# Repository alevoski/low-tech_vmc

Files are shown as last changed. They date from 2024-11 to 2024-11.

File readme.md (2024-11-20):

# low-tech_vmc




low-tech_vmc est un projet de construction de VMC double flux de façon low-tech.  
Ce repo présente essentiellement la partie électronique du projet, à base d'Arduino.

Pour avoir tout le détail, notamment la fabrication des caissons, voir cette page :  
https://wiki.lowtechlab.org/wiki/VMC_double_flux

Ce projet a commencé en Janvier 2023.  
C++ est utilisé pour l'ensemble du code source.  
C'est un projet finalisé sujet à des améliorations.

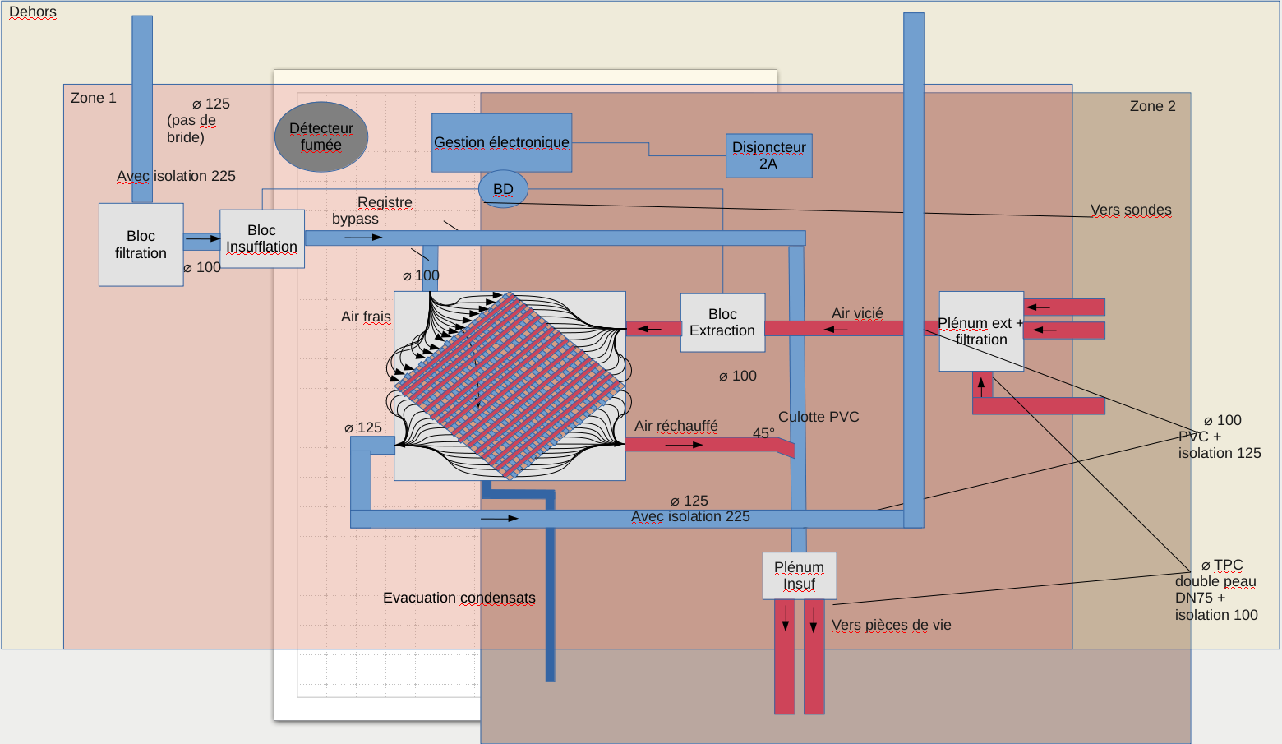
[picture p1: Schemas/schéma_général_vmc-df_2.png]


## Mise en garde
Attention à vous lors de la manipulation de la carte et des composants, notamment des ventilateurs et du relais !   
Cette installation est branchée sur le courant alternatif (220V) donc danger de mort si vous ne savez pas ce que vous faites !

Vous pouvez faire les tests sans brancher les ventilateurs. Les led du relais s'allumeront ou s'étendront en fonction du mode de fonctionnement (on/off) ce qui est suffisant pour un simple test.

## Compatibilité
Le code source a été testé avec succès avec les éléments suivants :
- un basic starter kit Arduino Uno R3 (contient la breadboard et les résistances nécessaires)
- une breadboard
- des résistances (1K, 3x 2K et 2x 10K)
- un module Bluetooth HC05
- trois sondes de températures DHT22
- un module relais double (circuit 12V pour les ventilateurs)
- deux ventilateurs Arctic P12 Max PWM
- une alimentation 12V 2A (pour les ventilateurs)
- une alimentation 9V 0.5A (pour la carte Arduino et les différents modules et les sondes)
- l'application Android Serial Bluetooth Terminal (pour télécommander)

Compilation : Arduino IDE sur Linux

## Mise en route
**Télécharger le projet sur votre ordinateur.**
```
git clone https://github.com/alevoski/low-tech_vmc.git
```

## Comment ça marche ?
Téléchargez Arduino IDE sur votre système puis : 

**Configurer le module BT**

Branchez votre carte et le module BT comme ceci :
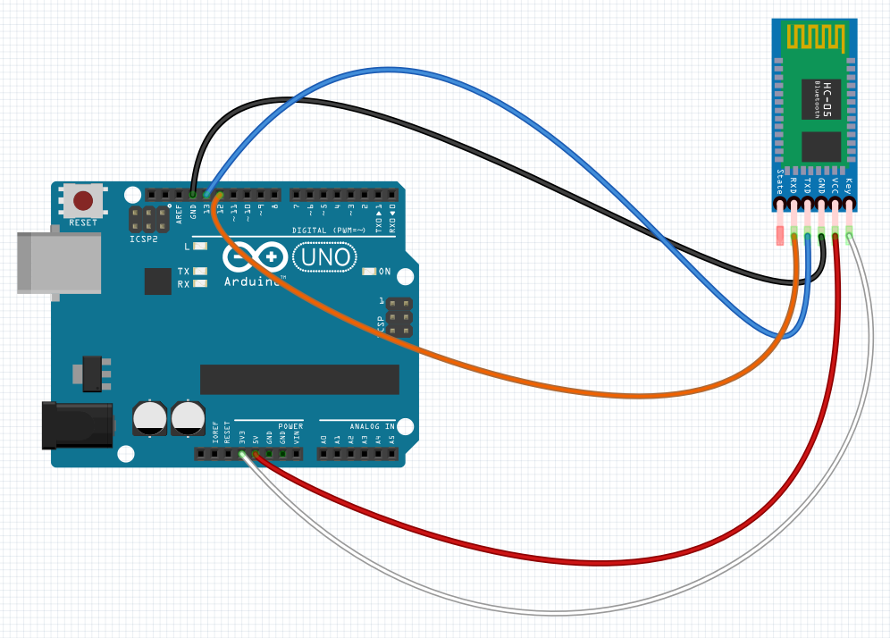
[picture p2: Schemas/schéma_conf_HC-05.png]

(ou voir le fichier Fritzing /Schema/config_BT2.fzz)

Puis ouvrez le ficher /CS/config_BT2/config_BT2.ino dans Arduino IDE.  
Branchez votre carte en USB sur votre ordinateur et compiler (Sketch -> Verify/Compile)

Détail complet ici :  
[lien](https://wiki.lowtechlab.org/wiki/VMC_double_flux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)

**Mise en place final**

Branchez votre carte avec les différents éléments comme ceci :
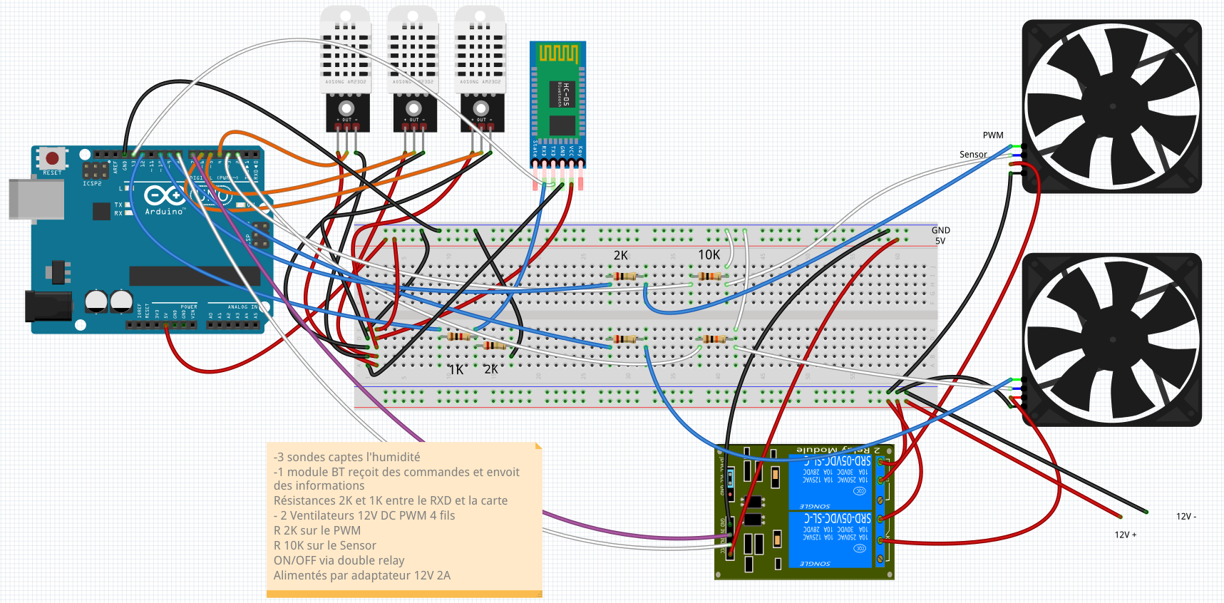
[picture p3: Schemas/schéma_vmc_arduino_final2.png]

(ou voir le fichier Fritzing /Schema/vmc_prefinal.fzz)

Puis ouvrez le fichier /CS/CS/vmc_final_v3/CS/vmc_final_v3.ino dans Arduino IDE.  
Branchez votre carte en USB sur votre ordinateur et compiler (Sketch -> Verify/Compile)

Détail complet ici :  
[lien](https://wiki.lowtechlab.org/wiki/VMC_double_flux#%C3%89tape_9_-_Gestion_%C3%A9lectronique_-_mise_en_place)

**Test**  

La carte Arduino doit être alimenter soit via USB soit via un adaptateur secteur.  
Vous n'êtes pas obligé de brancher les ventilateurs ici pour faire le test.

Etapes :
- Télécharger l'application Serial Bluetooth Terminal
- Liez votre smartphone au module HC-05
- Ouvrez l'application
- Sélectionner le device correspondant à votre module HC-05
- Connectez-vous à lui
- Tapez 'h' pour avoir la liste des fonctionnalités
- A vous de les tester une à une
- Vous pouvez configurer des boutons dans cette application pour vos usages récurrents

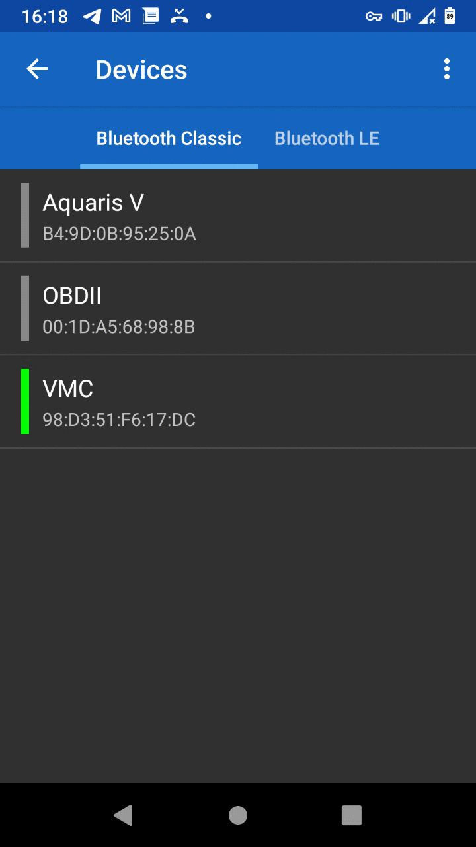
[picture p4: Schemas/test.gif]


Détail complet ici :  
[lien](https://wiki.lowtechlab.org/wiki/VMC_double_flux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)

## Auteur
Alexandre Buissé

## License
low-tech_vmc. VMC double flux low-tech.  
Copyright (C) 2024 Alexandre Buissé alevoski@pm.me

This program is free software: you can redistribute it and/or modify  
it under the terms of the GNU Affero General Public License as published  
by the Free Software Foundation, either version 3 of the License, or  
(at your option) any later version.  

This program is distributed in the hope that it will be useful,  
but WITHOUT ANY WARRANTY; without even the implied warranty of  
MERCHANTABILITY or FITNESS FOR A PARTICULAR PURPOSE.  See the  
GNU Affero General Public License for more details.  

You should have received a copy of the GNU Affero General Public License  
along with this program.  If not, see <https://www.gnu.org/licenses/>.

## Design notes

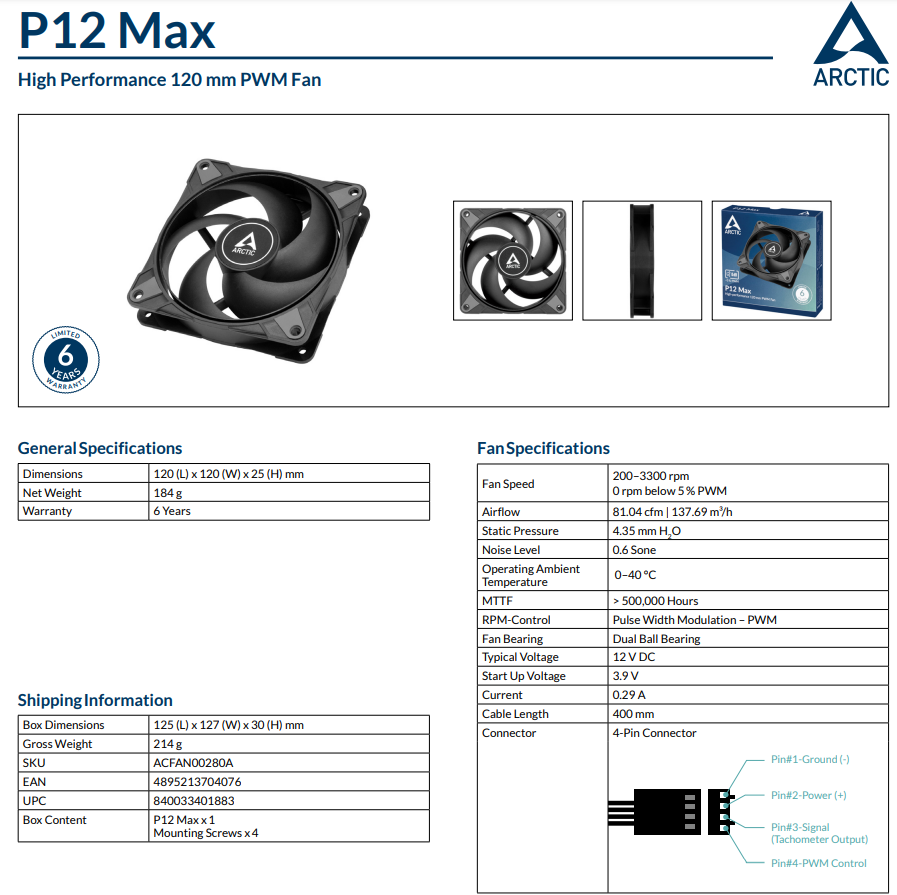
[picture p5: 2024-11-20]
Fan_specs/fan_p12max.png

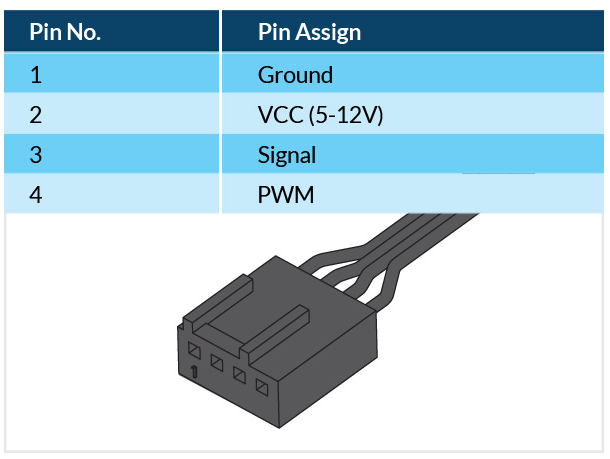
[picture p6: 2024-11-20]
Fan_specs/fan_p12max-connection.png

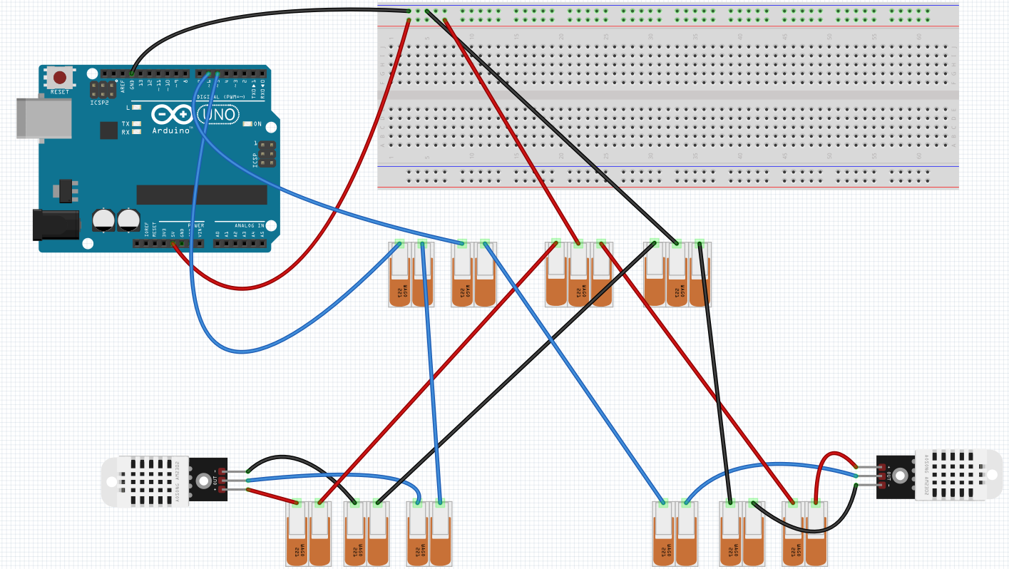
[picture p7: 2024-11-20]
Schemas/schéma_DHT22.png

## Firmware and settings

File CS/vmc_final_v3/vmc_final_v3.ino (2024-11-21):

/*
Ma VMC double flux
Alexandre Buissé
2023/04/13
*/

// Import des bibliotheques
#include <DHT.h>
#include <SoftwareSerial.h>

// Pins d'interruptions relay des ventilateurs
const int OUT_FAN_PIN = 7;
const int IN_FAN_PIN = 8;

// Pins PWM et RPM des ventilateurs
const int OUT_PWM_PIN = 9;
const int OUT_SENSOR_PIN = 2;
const int IN_PWM_PIN = 10;
const int IN_SENSOR_PIN = 3;

// Pins et types des sondes DHT
const int DHT1PIN = 4; // pour temp extérieur à l'insuflation
const int DHT2PIN = 5;
const int DHT3PIN = 6;
#define DHT1TYPE DHT22
#define DHT2TYPE DHT22
#define DHT3TYPE DHT22

// Pins de HC05
const int RXPIN = 13;
const int TXPIN = 12;

// Commmandes
const char CMD_BUTTON_0 = '0';
const char CMD_BUTTON_1 = '1';
const char CMD_BUTTON_2 = '2';
const char CMD_BUTTON_3 = '3';
const char CMD_BUTTON_4 = '4';
const char CMD_BUTTON_5 = '5';
const char CMD_BUTTON_6 = '6';
const char CMD_BUTTON_7 = '7';
const char CMD_BUTTON_S = 's';
const char CMD_BUTTON_B = 'b';
const char CMD_BUTTON_P = '+';
const char CMD_BUTTON_M = '-';
const char CMD_BUTTON_INFO = 'i';

// Initialisation des sondes DHT
DHT dht1(DHT1PIN, DHT1TYPE);
DHT dht2(DHT2PIN, DHT2TYPE);
DHT dht3(DHT3PIN, DHT3TYPE);

// Initialisation du HC05
SoftwareSerial mySerial(RXPIN, TXPIN);

// Définitions des variables
float vitesse = 0;
float old_vitesse_e = 0;
float old_vitesse_i = 0;
float vitesse_e = 0;
float vitesse_i = 0;
int mode = 1; // par défaut la ventilation est allumée
int sonde = 0;

void setup() {
  // Initialisation
  
  // Sondes DHT
  dht1.begin();
  dht2.begin();
  dht3.begin();

  // HC05
  pinMode(RXPIN, INPUT);
  pinMode(TXPIN, OUTPUT);

  // Ventilateurs
  
  // Configure Timer 1 for PWM @ 25 kHz.
  TCCR1A = 0;           // undo the configuration done by...
  TCCR1B = 0;           // ...the Arduino core library
  TCNT1  = 0;           // reset timer
  TCCR1A = _BV(COM1A1)  // non-inverted PWM on ch. A
         | _BV(COM1B1)  // same on ch; B
         | _BV(WGM11);  // mode 10: ph. correct PWM, TOP = ICR1
  TCCR1B = _BV(WGM13)   // ditto
         | _BV(CS10);   // prescaler = 1
  ICR1   = 320;         // TOP = 320

  // ON/OFF
  pinMode(OUT_FAN_PIN, OUTPUT);
  pinMode(IN_FAN_PIN, OUTPUT);
  digitalWrite(OUT_FAN_PIN, HIGH);
  digitalWrite(IN_FAN_PIN, HIGH);
  // Gestion de la vitesse
  pinMode(OUT_PWM_PIN, OUTPUT);
  pinMode(IN_PWM_PIN, OUTPUT);
  
  mySerial.begin(9600);
  Serial.begin(9600);

}

void loop() {
  
  int res = 0;
  int rpm = 0;
  int rpm_e = 0;
  int rpm_i = 0;
  float temp_moy;
  float hygrometrie_moy;
  float ext_temp;
  float ext_hygro;
  bool receive = false;
  char raw_message = "";
  char message = 'a';
  
  // Si CMD_BUTTON_O ou CMD_BUTTON_1 ou CMD_BUTTON_S enclenché juste avant, on boucle sur le mode auto ou le mode 2
  if (mode == 1 || mode == 2){

    res = getHumidity(1);
    
    ext_temp = getTemp(dht1);
    Serial.println((String)"Température extérieure : "+int(ext_temp)+" °C."); 
    
    if (ext_temp >= 1) {
      if (mode == 1) {
        Serial.println(F("Test ok mode 1"));
       
        vitesse = automode(res);
        vitesse_e = vitesse;
        vitesse_i = vitesse-30;
      }
      
      if (mode == 2) {
        Serial.println(F("Test ok mode 2"));
        vitesse = 70;
        vitesse_e = vitesse;
        vitesse_i = vitesse-30;
      }

      rpm_e = get_speed(int(vitesse_e));
      rpm_i = get_speed(int(vitesse_i));

      Serial.println((String)"Vitesse d'extraction : "+rpm_e+" rpm.");
      Serial.println((String)"Vitesse d'insufflation : "+rpm_i+" rpm.");
    }
    else {
      // on coupe la VMC, même l'extraction car risque de gel des condensats
      vitesse_e = 0;
      vitesse_i = 0;
      rpm_e = 0;
      rpm_i = 0;
      Serial.println((String)"Température extérieur trop faible pour démarrer la VMC ("+float(ext_temp)+" °C)");
    }
  }
  
  // On attend de recevoir un message (sans bloquer le programme)
  if (mySerial.available()) {
    raw_message = mySerial.read();
    message = msgFilter(raw_message);
    if (message != 'a') {
      receive = true;
    }
    else {
      return;
    }
  }

  if (message == CMD_BUTTON_0) {
    // Si VMC éteinte, on allume en mode automatique
    if (vitesse == 0){
      Serial.println(F("Allumage en mode automatique."));
      mySerial.println(F("Allumage en mode automatique."));
      
      res = getHumidity(1);
      ext_temp = getTemp(dht1);
      
      vitesse = automode(res);
      vitesse_e = vitesse;
      vitesse_i = vitesse-30;
      rpm_e = get_speed(int(vitesse_e));
      rpm_i = get_speed(int(vitesse_i));

      hygrometrie_moy = getHumidity(2);
      Serial.println((String)"Hygrométrie moyenne : "+int(hygrometrie_moy)+" %.");
      mySerial.println((String)"Hygrométrie moyenne : "+int(hygrometrie_moy)+" %.");
      
      Serial.println((String)"Vitesse d'extraction : "+rpm_e+" rpm.");
      mySerial.println((String)"Vitesse d'extraction : "+rpm_e+" rpm.");
      Serial.println((String)"Vitesse d'insufflation : "+rpm_i+" rpm.");
      mySerial.println((String)"Vitesse d'insufflation : "+rpm_i+" rpm.");

      Serial.println((String)"Température extérieure : "+int(ext_temp)+" °C.");
      mySerial.println((String)"Température extérieure  : "+int(ext_temp)+" °C.");

      mode = 1;
    }
    // Si VMC allumée, on l'éteint
    else{
      Serial.println(F("Arrêt de la VMC."));
      mySerial.println(F("Arrêt de la VMC."));

      digitalWrite(OUT_FAN_PIN, LOW);
      digitalWrite(IN_FAN_PIN, LOW);

      vitesse = 0;
      mode = -1;
    }

  }    
    
  else if (message == CMD_BUTTON_1) {
    if (mode != 1) {
      Serial.println(F("Mode automatique."));
      mySerial.println(F("Mode automatique."));
      // mode automatique
      res = getHumidity(1);
      vitesse = automode(res);
      vitesse_e = vitesse;
      vitesse_i = vitesse-30;
      rpm_e = get_speed(int(vitesse_e));
      rpm_i = get_speed(int(vitesse_i));
      Serial.println((String)"Vitesse d'extraction : "+rpm_e+" rpm.");
      mySerial.println((String)"Vitesse d'extraction : "+rpm_e+" rpm.");
      Serial.println((String)"Vitesse d'insufflation : "+rpm_i+" rpm.");
      mySerial.println((String)"Vitesse d'insufflation : "+rpm_i+" rpm.");
  
      hygrometrie_moy = getHumidity(2);
      Serial.println((String)"Hygrométrie moyenne : "+int(hygrometrie_moy)+" %.");
      mySerial.println((String)"Hygrométrie moyenne : "+int(hygrometrie_moy)+" %.");
    
    }
    else {
      Serial.println(F("Mode automatique déjà activé."));
      mySerial.println(F("Mode automatique déjà activé."));
    }
    
    mode = 1;
  }
  
  else if (message == CMD_BUTTON_P) {
    Serial.println(F("Vitesse +"));
    mySerial.println(F("Vitesse +"));
    if (vitesse < 91){
      vitesse = vitesse+10; // on augmente par palier de 10
      vitesse_e = vitesse;
      vitesse_i = vitesse-30;

      // Si on a dépassé les 91% on force à 91%
      if (vitesse > 91){
        vitesse = 91;
        vitesse_e = vitesse;
        vitesse_i = vitesse-30;
      }
      rpm_e = get_speed(int(vitesse_e));
      rpm_i = get_speed(int(vitesse_i));
      Serial.println((String)"Vitesse d'extraction : "+rpm_e+" rpm.");
      mySerial.println((String)"Vitesse d'extraction : "+rpm_e+" rpm.");
      Serial.println((String)"Vitesse d'insufflation : "+rpm_i+" rpm.");
      mySerial.println((String)"Vitesse d'insufflation : "+rpm_i+" rpm.");
    }
    else{
      Serial.println("Vitesse maximum atteinte !");
      mySerial.println("Vitesse maximum atteinte !");
    }

    mode = 0;
  }
    
  else if (message == CMD_BUTTON_M) {
    Serial.println(F("Vitesse -"));
    mySerial.println(F("Vitesse -"));
    if (vitesse > 35 && vitesse_i > 5){
      vitesse = vitesse-10; // on diminue par palier de 10
      vitesse_e = vitesse;
      vitesse_i = vitesse-30;
      rpm_e = get_speed(int(vitesse_e));
      rpm_i = get_speed(int(vitesse_i));
      Serial.println((String)"Vitesse d'extraction : "+rpm_e+" rpm.");
      mySerial.println((String)"Vitesse d'extraction : "+rpm_e+" rpm.");
      Serial.println((String)"Vitesse d'insufflation : "+rpm_i+" rpm.");
      mySerial.println((String)"Vitesse d'insufflation : "+rpm_i+" rpm.");
    }
    else{
      vitesse = 35;
      vitesse_e = vitesse;
      vitesse_i = vitesse-30;
      Serial.println(F("Vitesse minimum atteinte !"));
      mySerial.println(F("Vitesse minimum atteinte !"));
    }  

    mode = 0;
  }

  else if (message == CMD_BUTTON_2) {
    Serial.println(F("Vitesse + extraction"));
    mySerial.println(F("Vitesse + extraction"));
    if (vitesse_e < 91){
      vitesse_e = vitesse_e+10; // on augmente par palier de 10

      // Si on a dépassé les 91% on force à 91%
      if (vitesse_e > 91){
        vitesse_e = 91;
      }
      rpm = get_speed(int(vitesse_e));
      Serial.println((String)"Nouvelle vitesse extraction : "+rpm+" rpm.");
      mySerial.println((String)"Nouvelle vitesse extraction : "+rpm+" rpm.");
    }
    else{
      Serial.println("Vitesse maximum d'extraction atteinte !");
      mySerial.println("Vitesse maximum d'extraction atteinte !");
    }

    mode = 0;
  }

  else if (message == CMD_BUTTON_3) {
    Serial.println(F("Vitesse - extraction"));
    mySerial.println(F("Vitesse - extraction"));
    if (vitesse_e > 35){
      vitesse_e = vitesse_e-10; // on diminue par palier de 10

      // Si on a dépassé les 35% on force à 35%
      if (vitesse_e < 35){
        vitesse_e = 35;
      }
      
      rpm = get_speed(int(vitesse_e));
      Serial.println((String)"Nouvelle vitesse extraction : "+rpm+" rpm.");
      mySerial.println((String)"Nouvelle vitesse extraction: "+rpm+" rpm.");
    }
    else{
      vitesse_e = 35;
      Serial.println(F("Vitesse minimum d'extraction atteinte !"));
      mySerial.println(F("Vitesse minimum d'extraction atteinte !"));
    }  

    mode = 0;
  }

  else if (message == CMD_BUTTON_4) {
    Serial.println(F("Vitesse + insuflation"));
    mySerial.println(F("Vitesse + insuflation"));
    if (vitesse_i < 91){
      vitesse_i = vitesse_i+10; // on augmente par palier de 10

      // Si on a dépassé les 91% on force à 91%
      if (vitesse_i > 91){
        vitesse_i = 91; //~ 3003 RPM
      }
      rpm = get_speed(int(vitesse_i));
      Serial.println((String)"Nouvelle vitesse insuflation : "+rpm+" rpm.");
      mySerial.println((String)"Nouvelle vitesse insuflation : "+rpm+" rpm.");
    }
    else{
      Serial.println("Vitesse maximum d'insuflation atteinte !");
      mySerial.println("Vitesse maximum d'insuflation atteinte !");
    }

    mode = 0;
  }

  else if (message == CMD_BUTTON_5) {
    Serial.println(F("Vitesse - insuflation"));
    mySerial.println(F("Vitesse - insuflation"));
    if (vitesse_i > 5){
      vitesse_i = vitesse_i-10; // on diminue par palier de 10
      
      // Si on a dépassé les 5% on force à 5%
      if (vitesse_i < 5){
        vitesse_i = 5;
      }
      
      rpm = get_speed(int(vitesse_i));
      Serial.println((String)"Nouvelle vitesse insuflation : "+rpm+" rpm.");
      mySerial.println((String)"Nouvelle vitesse insuflation: "+rpm+" rpm.");
    }
    else{
      vitesse_i = 5; //~ 165 RPM
      Serial.println(F("Vitesse minimum d'insuflation atteinte !"));
      mySerial.println(F("Vitesse minimum d'insuflation atteinte !"));
    }  

    mode = 0;
  }
    
  else if (message == CMD_BUTTON_6) {
    if (digitalRead(OUT_FAN_PIN) == HIGH) {
      Serial.println(F("Bypass extraction."));
      mySerial.println(F("Bypass extraction."));
      digitalWrite(OUT_FAN_PIN, LOW);
    }
    else if (digitalRead(OUT_FAN_PIN) == LOW) {
      Serial.println(F("Marche extraction."));
      mySerial.println(F("Marche extraction."));
      digitalWrite(OUT_FAN_PIN, HIGH);
    }

    mode = 0;
  }
    
  else if (message == CMD_BUTTON_7) {
    if (digitalRead(IN_FAN_PIN) == HIGH) {
      Serial.println(F("Bypass insuflation."));
      mySerial.println(F("Bypass insuflation."));
      digitalWrite(IN_FAN_PIN, LOW);
    }
    else if (digitalRead(IN_FAN_PIN) == LOW) {
      Serial.println(F("Marche insuflation."));
      mySerial.println(F("Marche insuflation."));
      digitalWrite(IN_FAN_PIN, HIGH);
    }

    mode = 0;
  }

  else if (message == CMD_BUTTON_S) {
      
    if (vitesse != 70 && vitesse_i != (70-30)) {
      Serial.println(F("Mode silencieux"));
      mySerial.println(F("Mode silencieux"));

      vitesse = 70;
      vitesse_e = vitesse;
      vitesse_i = vitesse-30;
      rpm_e = get_speed(int(vitesse_e));
      rpm_i = get_speed(int(vitesse_i));
      Serial.println((String)"Vitesse d'extraction : "+rpm_e+" rpm.");
      Serial.println((String)"Vitesse d'insufflation : "+rpm_i+" rpm.");
      mySerial.println((String)"Vitesse d'extraction : "+rpm_e+" rpm.");
      mySerial.println((String)"Vitesse d'insufflation : "+rpm_i+" rpm.");             
    }
    
    else {
      Serial.println(F("Mode silencieux déjà activé"));
      mySerial.println(F("Mode silencieux déjà activé"));
    }
      
    mode = 2;
  }

  else if (message == CMD_BUTTON_B) {
    if (digitalRead(OUT_FAN_PIN) == LOW && digitalRead(IN_FAN_PIN) == LOW) {
      digitalWrite(OUT_FAN_PIN, HIGH);
      digitalWrite(IN_FAN_PIN, HIGH);
      }
    if (vitesse != 95) {
      Serial.println(F("Mode boost"));
      mySerial.println(F("Mode boost"));
    }
    else {
      Serial.println(F("Mode boost déjà activé"));
      mySerial.println(F("Mode boost déjà activé"));
    }
    
    vitesse = 95;
    vitesse_e = vitesse;
    vitesse_i = vitesse-30;
    rpm_e = get_speed(int(vitesse_e));
    rpm_i = get_speed(int(vitesse_i));
    Serial.println((String)"Vitesse d'extraction : "+rpm_e+" rpm.");
    mySerial.println((String)"Vitesse d'extraction : "+rpm_e+" rpm.");
    Serial.println((String)"Vitesse d'insufflation : "+rpm_i+" rpm.");
    mySerial.println((String)"Vitesse d'insufflation : "+rpm_i+" rpm.");
    mode = 0;
  }

  else if (message == CMD_BUTTON_INFO) {
    Serial.println(F("Etat de la ventilation"));
    Serial.println((String)"Mode : "+mode);
    mySerial.println(F("Etat de la ventilation"));
    mySerial.println((String)"Mode : "+mode);

    // Affichage du mode de fonctionnement
    if (mode == -1) {
      Serial.println(F("La VMC est à l'arrêt."));
      mySerial.println(F("La VMC est à l'arrêt."));
    }
    else if (mode == 0) {
      Serial.println(F("La VMC est en mode manuel."));
      mySerial.println(F("La VMC est en mode manuel."));
    }
    else if (mode == 1) {
      Serial.println(F("La VMC est en mode automatique."));
      mySerial.println(F("La VMC est en mode automatique."));
    }
    else if (mode == 2) {
      Serial.println(F("La VMC est en mode silencieux."));
      mySerial.println(F("La VMC est en mode silencieux."));
    }

    // Affichage du fonctionnement de la ventillation
    if (digitalRead(OUT_FAN_PIN) == LOW && digitalRead(IN_FAN_PIN) == LOW) {
      Serial.println(F("La VMC est à l'arrêt car la ventilation est en bypass."));
      mySerial.println(F("La VMC est à l'arrêt car la ventilation est en bypass."));
    }      
    else if (digitalRead(IN_FAN_PIN) == LOW) {
      Serial.println(F("L'insufflation est en bypass."));
      mySerial.println(F("L'insufflation est en bypass."));
      rpm_e = get_speed(int(vitesse_e));
      Serial.println((String)"Vitesse d'extraction : "+rpm_e+" rpm.");
      mySerial.println((String)"Vitesse d'extraction : "+rpm_e+" rpm.");
    }
    else if (digitalRead(OUT_FAN_PIN) == LOW) {
      Serial.println(F("L'extraction est en bypass."));
      mySerial.println(F("L'extraction est en bypass."));
      rpm_i = get_speed(int(vitesse_i));
      Serial.println((String)"Vitesse d'insufflation : "+rpm_i+" rpm.");
      mySerial.println((String)"Vitesse d'insufflation : "+rpm_i+" rpm.");
    }
    else{
      rpm_e = get_speed(int(vitesse_e));
      rpm_i = get_speed(int(vitesse_i));
      Serial.println((String)"Vitesse d'extraction : "+rpm_e+" rpm.");
      mySerial.println((String)"Vitesse d'extraction : "+rpm_e+" rpm.");
      Serial.println((String)"Vitesse d'insufflation : "+rpm_i+" rpm.");
      mySerial.println((String)"Vitesse d'insufflation : "+rpm_i+" rpm.");
    }

    // Affichage de l'hygrométrie/température moyenne et l'hygrométrie/température extérieure
    temp_moy = (getTemp(dht2) + getTemp(dht3))/2;
    Serial.println((String)"Température moyenne : "+float(temp_moy)+" °C.");
    mySerial.println((String)"Température moyenne  : "+float(temp_moy)+" °C.");
    
    hygrometrie_moy = getHumidity(2);
    Serial.println((String)"Hygrométrie moyenne : "+int(hygrometrie_moy)+" %.");
    mySerial.println((String)"Hygrométrie moyenne : "+int(hygrometrie_moy)+" %.");
    
    ext_temp = getTemp(dht1);
    Serial.println((String)"Température extérieure : "+float(ext_temp)+" °C.");
    mySerial.println((String)"Température extérieure  : "+float(ext_temp)+" °C.");
    if (ext_temp < 1) {
      mySerial.println((String)"Température extérieur trop faible pour démarrer la VMC ("+float(ext_temp)+" °C)");
    }

    ext_hygro = getHumidity(3);
    Serial.println((String)"Hygrométrie extérieure : "+int(ext_hygro)+" %.");
    mySerial.println((String)"Hygrométrie extérieure : "+int(ext_hygro)+" %.");
  }

  else if (message == 'h') {
    Serial.println(F("Manuel d'utilisation"));
    mySerial.println(F("Manuel d'utilisation"));
    mySerial.println(F("0 : ON/OFF"));
    mySerial.println(F("1 : Mode automatique"));
    mySerial.println(F("+ : Vitesse +"));
    mySerial.println(F("- : Vitesse -"));
    mySerial.println(F("2 : Vitesse + extraction"));
    mySerial.println(F("3 : Vitesse - extraction"));
    mySerial.println(F("4 : Vitesse + insuflation"));
    mySerial.println(F("5 : Vitesse - insuflation"));
    mySerial.println(F("6 : Bypass extraction"));
    mySerial.println(F("7 : Bypass insuflation"));
    mySerial.println(F("s : Mode silencieux"));
    mySerial.println(F("b : Mode boost"));
    mySerial.println(F("i : Etat de la ventilation"));
  }
    
  else if (receive == true && message != 'a') {
    Serial.println((String)"valid msg : "+message);
    if (message != 0 || message != 1 || message != 2 || message != 3 || 
    message != 4 || message != 5 || message != 6 || message != 7 || message != 'h' || message != '\r' || 
    message != '\n' || message != 's' || message != 'b') {
      Serial.println(F("La commande n'existe pas, envoyer 'h' pour recevoir le manuel d'utilisation"));
      mySerial.println(F("La commande n'existe pas, envoyer 'h' pour recevoir le manuel d'utilisation"));
    }
  }
       
  // changement de vitesse
  if (old_vitesse_e != vitesse_e) {
    Serial.println((String)"vitesse d'extraction actuelle : "+old_vitesse_e+" %.");
    // set la ventilation
    Serial.println((String)"changement de vitesse d'extraction à : "+int(vitesse_e)+" %.");
    pinMode(OUT_PWM_PIN, OUTPUT);
    analogWrite25k(OUT_PWM_PIN, int(vitesse_e*3.2));

    old_vitesse_e = vitesse_e;
  }
  if (old_vitesse_i != vitesse_i) {
    Serial.println((String)"vitesse d'insuflation actuelle : "+old_vitesse_i+" %.");
    // set la ventilation
    Serial.println((String)"changement de vitesse d'insuflation à : "+int(vitesse_i)+" %.");
    pinMode(IN_PWM_PIN, OUTPUT);
    analogWrite25k(IN_PWM_PIN, int(vitesse_i*3.2));

    old_vitesse_i = vitesse_i;

  }

  // Gestion du on/off des ventillateurs pour les modes 1 et 2
  // vitesse_i et vitesse_e sont mis à 0 dans ces modes si ext_temp < 1
  if (mode == 1 || mode == 2){
    // insufflation
    if (vitesse_i == 0 && digitalRead(IN_FAN_PIN) == HIGH) {
      digitalWrite(IN_FAN_PIN, LOW);
    }
    // pour rallumer le ventilateur 
    if (vitesse_i > 0 && digitalRead(IN_FAN_PIN) == LOW) {
      digitalWrite(IN_FAN_PIN, HIGH);
    }
  
    // extraction
    if (vitesse_e == 0 && digitalRead(OUT_FAN_PIN) == HIGH) {
      digitalWrite(OUT_FAN_PIN, LOW);
    }
    // pour rallumer le ventilateur 
    if (vitesse_e > 0 && digitalRead(OUT_FAN_PIN) == LOW) {
      digitalWrite(OUT_FAN_PIN, HIGH);
    }
  }

  delay(5000);

}

// Fonction msgFilter(raw_message) pour filter les commandes reçu, retourne un message filtré
char msgFilter(char raw_message) {
//  char okchar[] = "abcdefghijklmnopqrstuvwxyzABCDEFGHIJKLMNOPQRSTUVWXYZ0123456789";
  char message = 'a';

  Serial.println((String)"defaut msg : "+message);
  Serial.println((String)"raw_message : "+raw_message);
  Serial.println((String)"strlen(raw_message) : "+strlen(raw_message));

//  if (strlen(raw_message) == 1) { // not working
  if (isalpha(raw_message) || isdigit(raw_message) || raw_message == '-' || raw_message == '+') {
    message = char(raw_message);
  }

  Serial.println((String)"return msg : "+message);
  
  return message;
}

// Fonction getTemp(sonde) pour lire la température de la sonde en paramètre
// Retourne la température de la sonde
int getTemp(DHT sonde) {
  float temp = 0;

  temp = sonde.readTemperature();
  
  return temp;
}
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

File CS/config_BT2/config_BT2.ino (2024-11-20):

// Working to change name and password !
// https://forum.arduino.cc/t/hc-05-at-pswd-doesnt-save/965871/7

#include <SoftwareSerial.h>
SoftwareSerial Bluetooth(13,12);

char c=' ';
void setup() 
{
  Serial.begin(9600);
  Serial.println("ENTER AT COMMAND");
  Bluetooth.begin(38400);
}

void loop() 
{
  if(Bluetooth.available())
  {
    c=Bluetooth.read();
    Serial.write(c);
  }
  if(Serial.available())
  {
    c=Serial.read();
    Bluetooth.write(c);
  }
}

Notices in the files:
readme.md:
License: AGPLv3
